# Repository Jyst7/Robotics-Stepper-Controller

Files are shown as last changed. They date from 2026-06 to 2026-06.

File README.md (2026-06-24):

# Robotics-Stepper-Controller

Screenshot 2026-06-23 at 11 46 33 PM

Screenshot 2026-06-23 at 11 47 46 PM

Screenshot 2026-06-23 at 11 48 07 PM

Screenshot 2026-06-23 at 11 48 39 PM

This project is a motor controller board and a cycloidal gearbox. It is designed around the esp32 s3 and can handle up to 6 nema 23's using dm542's.

## Main features

- ESP32 S3: allows for wifi and bluetooth connectivity aswell as allows programming using arduino ide

- up to 6 motors: allows for using up to 60 motors through the dm542 motor driver

- up to 8 inputs: allows for some electrically isolated inputs for limit switches probes, etc

- Sd card: not to sure what to use it for at the moment but its useful to have

- 3d printed cycloidal reducer: 1:10 ratio cycloidal gearbox designed to mount to a Keling KL23H276-30-4A stepper motor

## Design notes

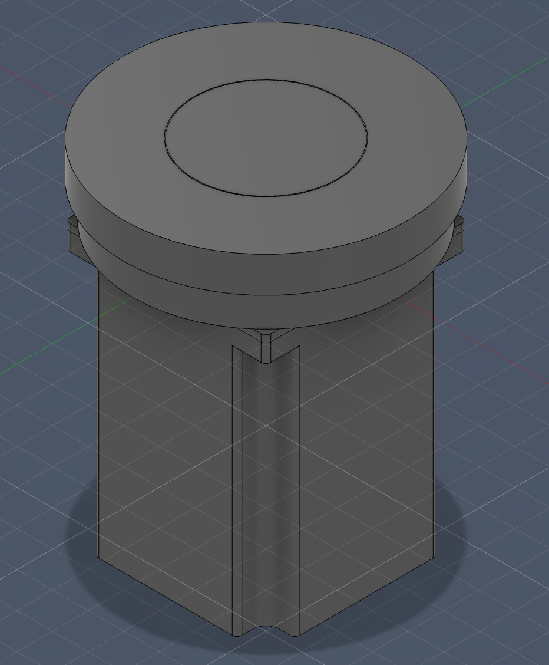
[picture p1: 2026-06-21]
Images/nema23-actuator.png

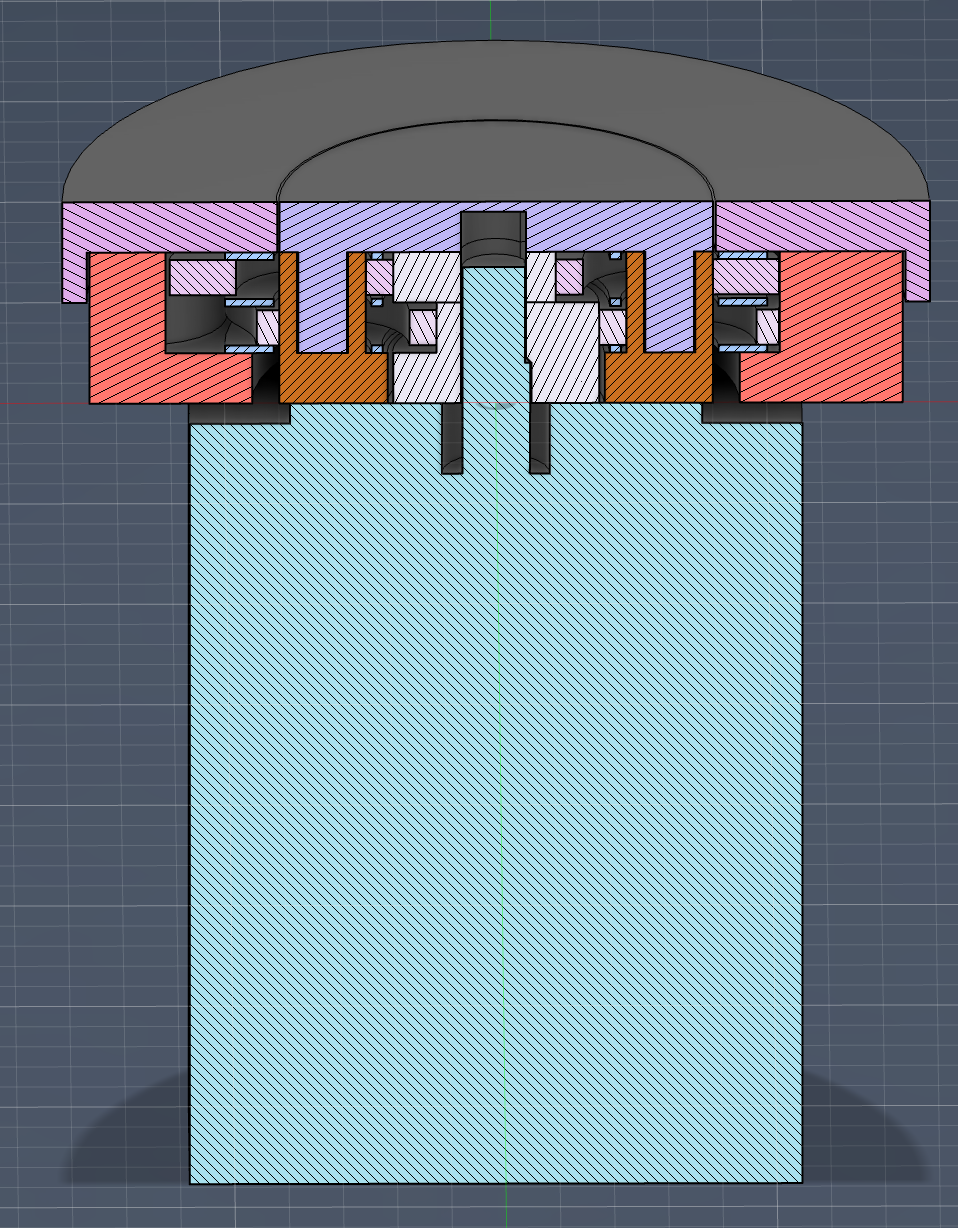
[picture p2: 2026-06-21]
Images/split-nema23-actuator.png

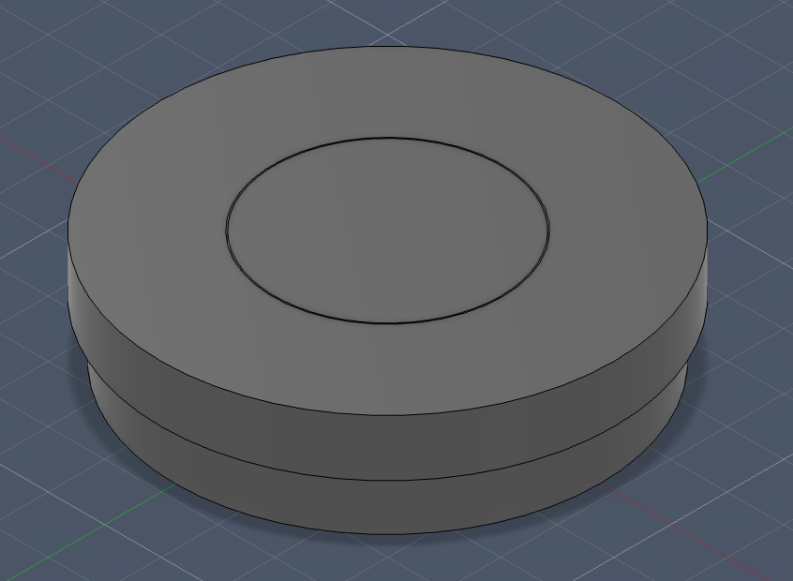
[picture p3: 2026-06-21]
Images/actuator.png

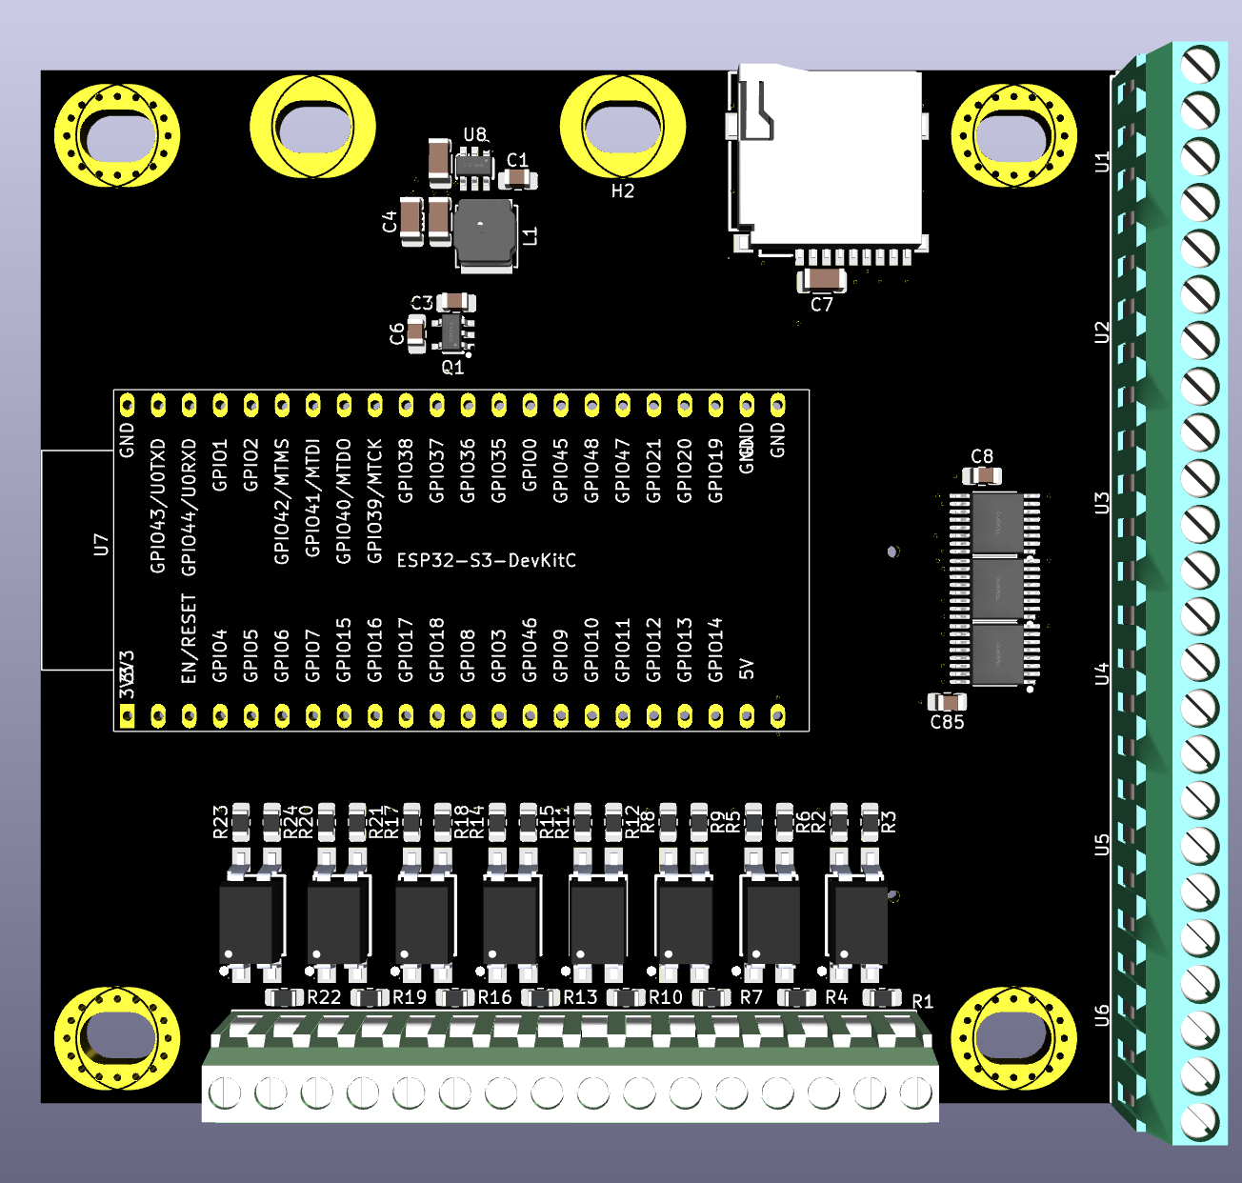
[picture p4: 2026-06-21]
Images/render-1.png

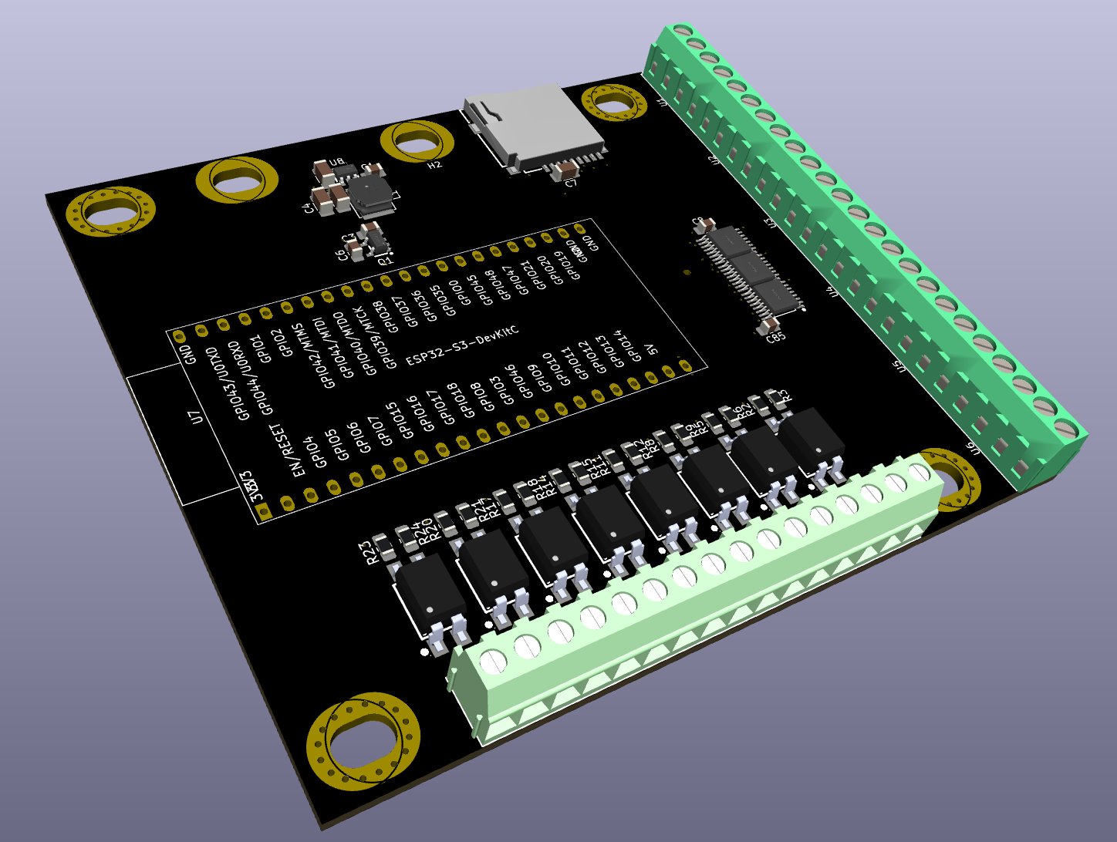
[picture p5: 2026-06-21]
Images/render-2.png

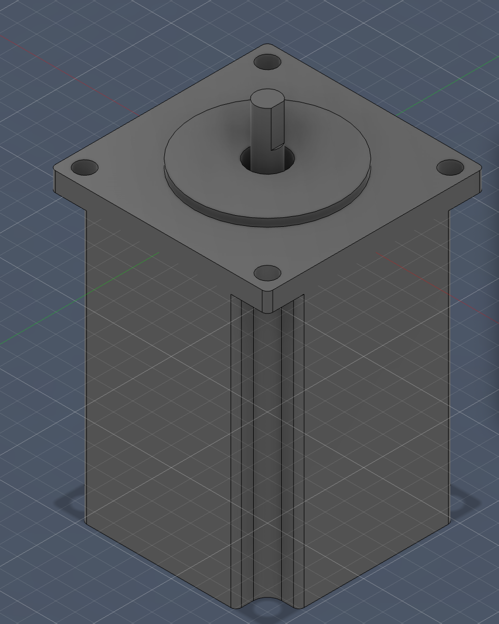
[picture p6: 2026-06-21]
Images/nema23.png

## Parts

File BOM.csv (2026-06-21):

BOM
Untitled
Reference | Qty | Value | DNP | Exclude from BOM | Exclude from Board | Footprint | Datasheet | LCSC Part | Price
U14,U18 | 2 | DB125-3.5-8P-GN-S |  |  |  | easyeda2kicad:CONN-TH_8P-P3.50_DORABO_DB125-3.5-8P-GN-S | https://www.lcsc.com/datasheet/C5184954.pdf | C5184954 | $1.30
U12,U16,U20 | 5 | 74AHCT595T16-13 |  |  |  | easyeda2kicad:TSSOP-16_L5.0-W4.4-P0.65-LS6.4-BL | https://lcsc.com/product-detail/presales_Diodes-Incorporated-74AHCT595T16-13_C460504.html | C460504 | $1.32
U10,U11,U13,U15,U17,U19,U21,U22 | 10 | TLP521GB-S_C20612587 |  |  |  | easyeda2kicad:SMD-4_L6.5-W4.6-P2.54-LS10.2-BL | https://www.lcsc.com/datasheet/C20612587.pdf | C20612587 | $1.10
U8 | 1 | AP63205WU-7 |  |  |  | easyeda2kicad:TSOT-23-6_L2.9-W1.6-P0.95-LS2.8-BL | https://www.lcsc.com/datasheet/C2071056.pdf | C2071056 | $0.44
U7 | 5 | ESP32-S3-DevKitC(PIN HEADERS) |  |  |  | PCM_Espressif:ESP32-S3-DevKitC | https://www.lcsc.com/datasheet/C7499337.pdf | C7499337 | $0.93
U1,U2,U3,U4,U5,U6 | 10 | DB125-3.5-4P-GN |  |  |  | easyeda2kicad:CONN-TH_DB125-3.5-4P-GN | https://www.lcsc.com/datasheet/C2757925.pdf | C2757925 | $3.37
R3,R6,R9,R12,R15,R18,R21,R24 | 20 | 10K |  |  |  | Resistor_SMD:R_0805_2012Metric_Pad1.20x1.40mm_HandSolder | https://www.lcsc.com/datasheet/C110775.pdf | C110775 | $0.78
R2,R5,R8,R11,R14,R17,R20,R23 | 20 | 1K |  |  |  | Resistor_SMD:R_0805_2012Metric_Pad1.20x1.40mm_HandSolder | https://www.lcsc.com/datasheet/C110774.pdf | C110774 | $0.79
R1,R4,R7,R10,R13,R16,R19,R22 | 10 | 300Ω |  |  |  | Resistor_SMD:R_0805_2012Metric_Pad1.20x1.40mm_HandSolder | https://www.lcsc.com/datasheet/C7603206.pdf | C7603206 | $3.45
Q1 | 1 | XC6220B331MR-G |  |  |  | easyeda2kicad:SOT-25_L3.0-W1.6-P0.95-LS2.8-TL | https://lcsc.com/product-detail/Low-Dropout-Regulators-LDO_XC6220B331MR-G_C86534.html | C86534 | $0.45
L1 | 10 | 4.7μH |  |  |  | easyeda2kicad:IND-SMD_L5.0-W5.0 | https://www.lcsc.com/datasheet/C520348.pdf | C520348 | $0.56
Card1 | 10 | TF PUSH |  |  |  | easyeda2kicad:TF-SMD_TF-PUSH | https://lcsc.com/product-detail/Connector-Card-Sockets_SHOU-HAN-SHOU-HAN-TFDeck-TF-Deck_C393941.html | C393941 | $1.26
C1,C7,C8,C85 | 50 | 0.1 μF |  |  |  | Capacitor_SMD:C_0805_2012Metric_Pad1.18x1.45mm_HandSolder | https://www.lcsc.com/datasheet/C49678.pdf | C49678 | $1.34
C7 | 50 | 100nF |  |  |  | Capacitor_SMD:C_1206_3216Metric | https://www.lcsc.com/datasheet/C309030.pdf | C309030 | $1.28
C6 | 10 | 4.7μF |  |  |  | Capacitor_SMD:C_0805_2012Metric_Pad1.18x1.45mm_HandSolder | https://www.lcsc.com/datasheet/C33546011.pdf | C33546011 | $0.78
C4,C5 | 10 | 22μF |  |  |  | Capacitor_SMD:C_1206_3216Metric | https://www.lcsc.com/datasheet/C342620.pdf | C342620 | $3.61
C2,C3 | 20 | 10μF |  |  |  | Capacitor_SMD:C_0805_2012Metric_Pad1.18x1.45mm_HandSolder | https://www.lcsc.com/datasheet/C1713.pdf | C1713 | $0.98
Total LCSC |  |  |  |  |  |  |  |  | $23.74
DM542 | 6 |  |  |  |  |  | https://www.aliexpress.com/item/1005005264850020.html |  | $32.94
Total Aliexpress |  |  |  |  |  |  |  |  | $32.94
Total Overall |  |  |  |  |  |  |  |  | $56.68

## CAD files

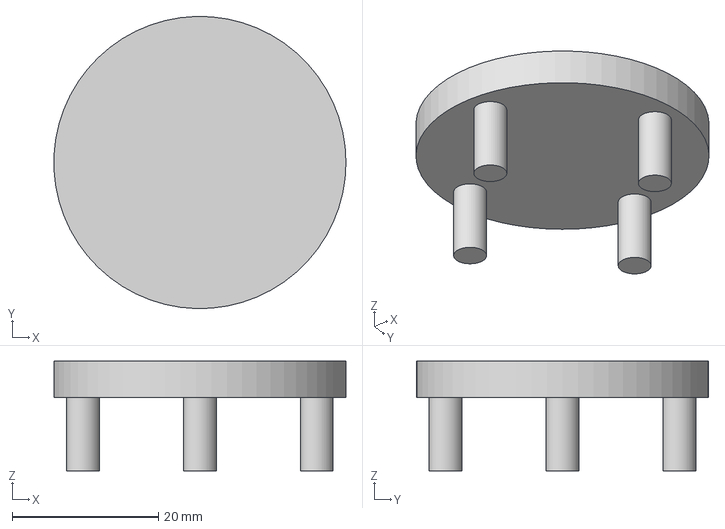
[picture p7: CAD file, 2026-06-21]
CAD/Component16.step
40.0 x 40.0 x 15.0 mm

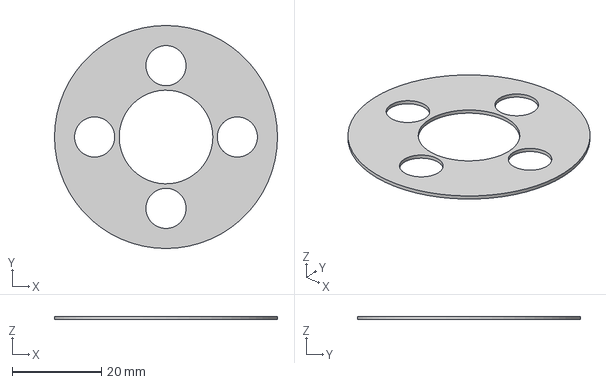
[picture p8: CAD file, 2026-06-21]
CAD/Spacer.step
50.0 x 50.0 x 0.75 mm

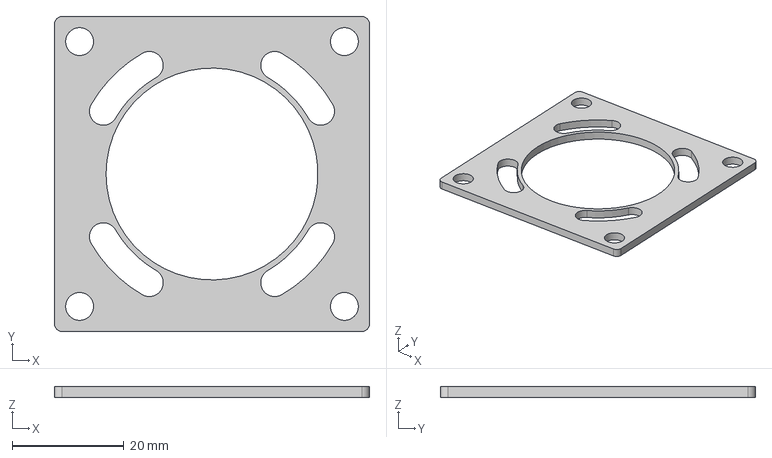
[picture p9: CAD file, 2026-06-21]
CAD/Cycloidal Drive.step
56.5 x 56.5 x 2.00 mm

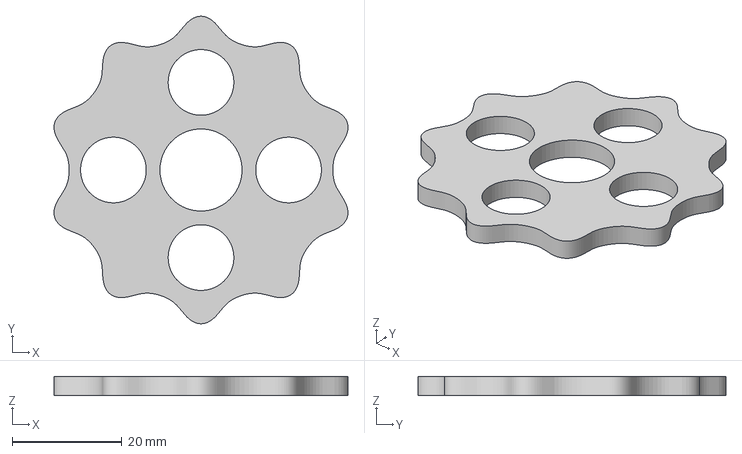
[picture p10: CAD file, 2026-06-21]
CAD/Component13.step
53.7 x 56.2 x 3.50 mm

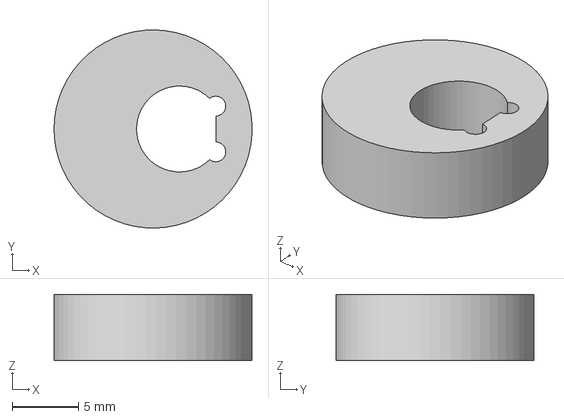
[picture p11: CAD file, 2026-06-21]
CAD/Component12-1.step
15.0 x 15.0 x 5.00 mm

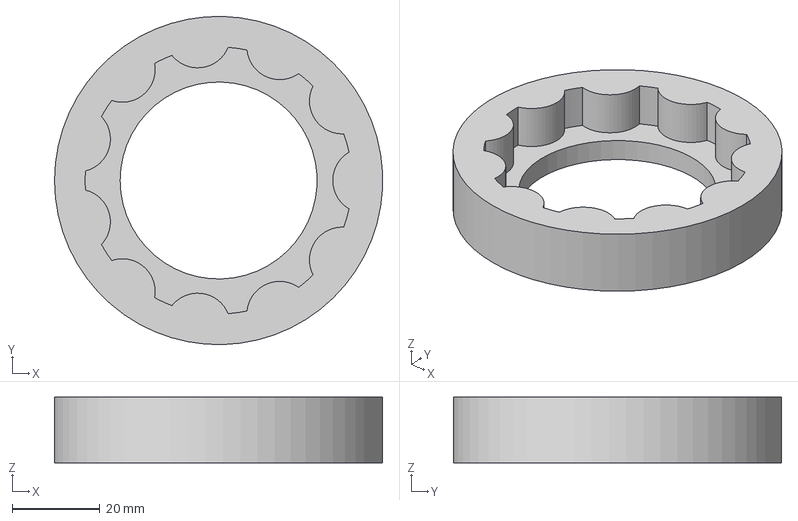
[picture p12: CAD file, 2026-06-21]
CAD/Component10.step
74.9 x 75.0 x 15.0 mm

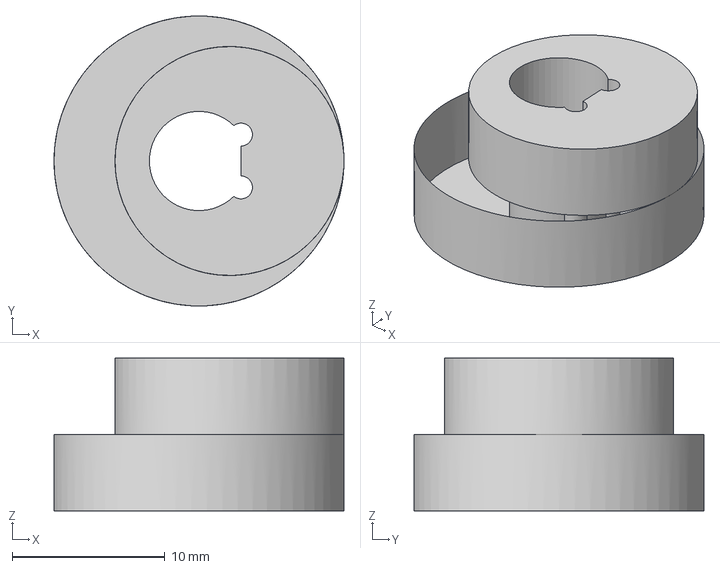
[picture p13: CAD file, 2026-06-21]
CAD/Component12.step
19.0 x 19.0 x 10.0 mm

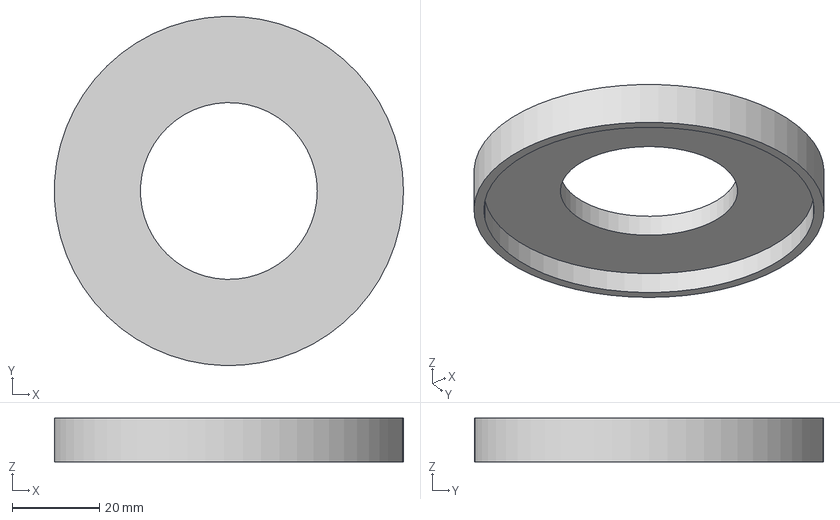
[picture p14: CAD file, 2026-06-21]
CAD/Component15.step
79.9 x 80.0 x 10.0 mm

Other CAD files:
CAD/Component11.step

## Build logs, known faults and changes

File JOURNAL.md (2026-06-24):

## Background - 0 Hours

The reason I decided to make this project was for two reasons, the first being I wanted to justify procrastinating studying for exams and I'd feel bad if I was just doomscrolling and the second is because I had 3 stepper motors lying around specifically the Keling Technology, Inc Hybrid Stepper Motor Type:KL23H276-30-4A. I would like to be able to use them and I recently got a power supply. I didn't really have any large constrainst for this project but I knew that I wanted to have the ability to add more motors later on as well as other peripherals that I might use in the future. I also wanted to under the guise of this project to make some simple cycloidal drives for the motors and see the extent of their strength. I later in the process decided it might be nice to attempt to turn this into a robotic arm because I find them cool, which in my opionion is a great reason. Also all parts should be purchased from Aliexpress, Lcsc, and Jlcpcb. I somehow forgot about the biggest constraint of all which is money, the goal is to keep it under $120 but if absolutely necessary could be stretched to $180 as I am making this for hackclub's outpost ysws.

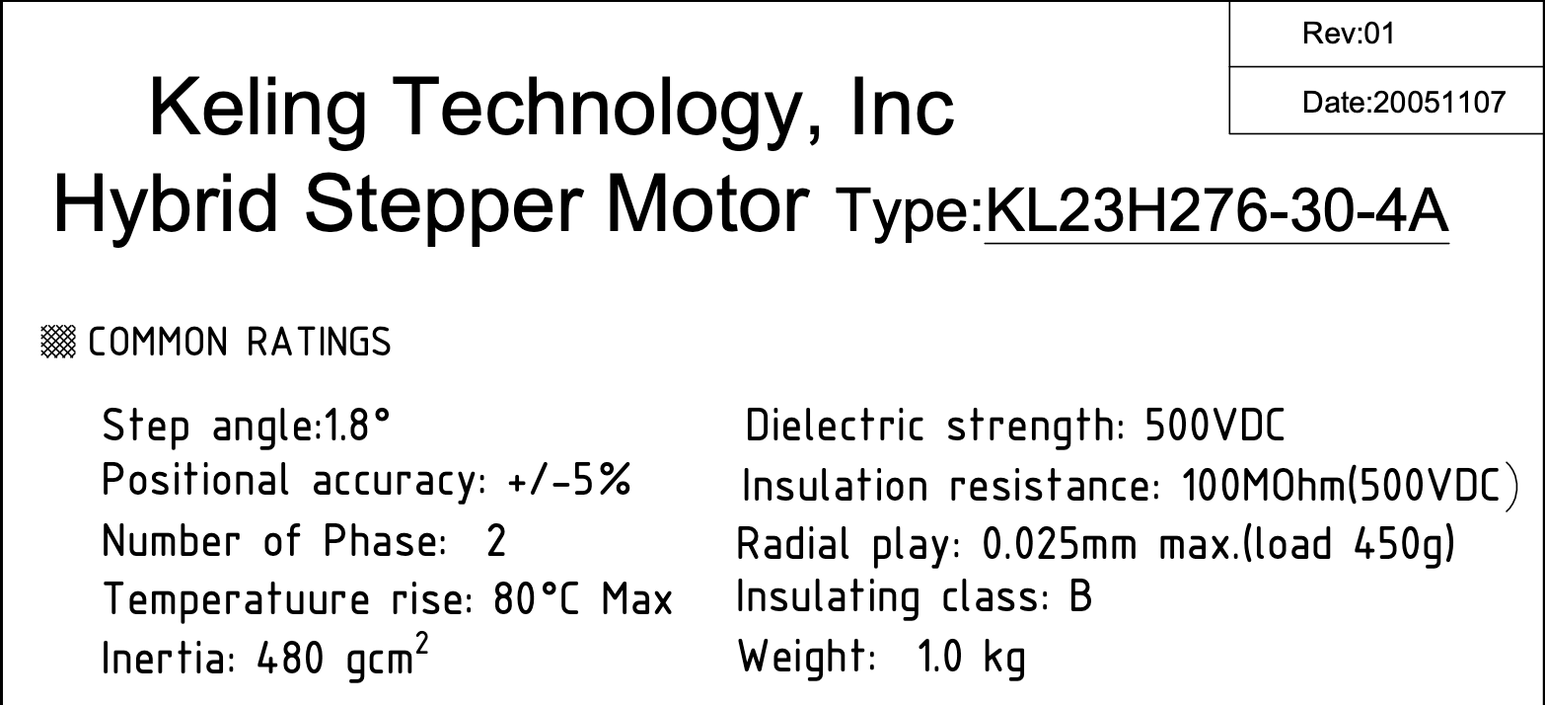
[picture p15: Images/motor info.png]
motor info


## Research - 3 Hours

The first thing I wanted to reasearch was the motor drivers I was going to use. I took a look at aliexpress just searching up stepper motor drivers and saw three different options which went down to two when I realized for this big motor it probably needs a decently large stepper driver for the heat and other things. So I threw all the data about the motors into google and apparently it is quite close to being a nema 23 motor which I found slightly weird based on the size differences, but google probably knows better than me because its twice the size of a nema 17. So the two motor drivers I decided between was the TB6600 and the DM542. It was not very difficult to decide between the two as almost every source online unanimously says the DM542 is better.

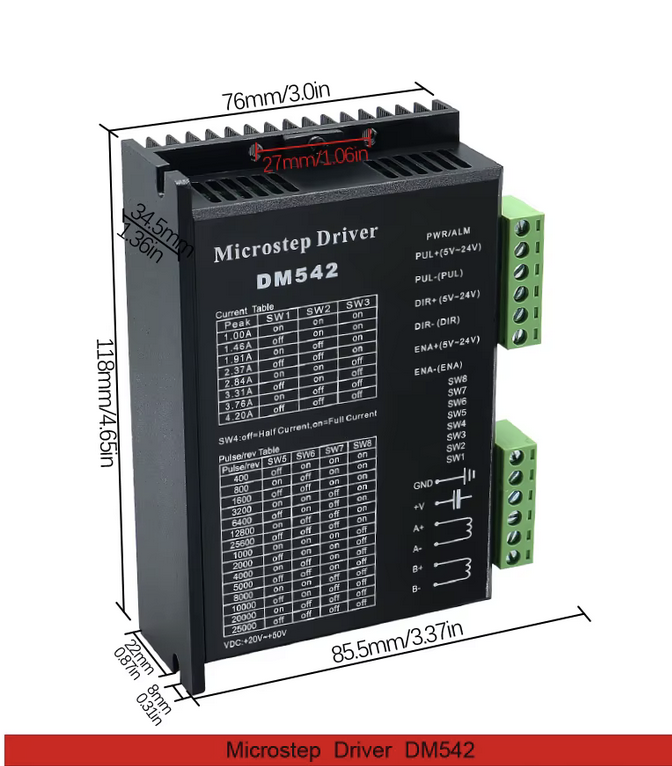
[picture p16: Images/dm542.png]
motor driver


I also took a look at many other different cnc controllers as I made the assumption that the board I am making is just a cnc controller without the logic and circuits for the spindle motor. I also was able to look at the controller boards for the large cnc machine and the small one that is in the shop at my school and other than the integrated psu and spindle motor stuff I had a good idea of what I needed to make to the board.

The microcontroller that I decided on was the esp32 s3 devkitc. Not only is this a decently powerful microcontroller, but it works with Arduino IDE which I found has integrated libraries for using stepper motors with the DM542. What was even better is I have two of these on hand so I could save some of my budget for other things. The esp32 also has integrated bluetooth and wifi capabilities so I could potentially make a webapp or something of the sort to connect to it and send commands to the motors, but the implementation for that will be later for now the goal is getting the motors to spin up.

Thinking about my 3d printer I decided an sd card is good to have because you never know when the need for the sd card could come up so some precautionary work is always good to have done.

I also wanted some optocouplers because I had seen them on some other boards and the purpose of them seems quite useful. They should mostly be electrically isolated from the rest of the board other than the 5v power which is fine so if something goes wrong and dumps a ton of voltage or current the optocoupler breaks or the 5v converter breaks and not the rest of the board. Thus allowing for safe addition of other inputs such as limit switches to not crash an axis if I'm doing something that has an axis, or probing a point in space.

For the power situation I decided to underpower my motors a bit because my psu can safely go up to 32V which is I believe the reccomended amound for nema 23 motors I didn't really want to go near the top range of my PSU's capabilities so I thought 24V would work fine they just wouldn't be as powerful as they could be. This also made powering the pcb slightly easier as I already had a buck converter in mind. So I would take the 24V from the psu and buck it down to 5V which can power some things that are fine with a bit of noise and then I could use an LDO to get a clean 3.3v to the SD card and the esp32 which don't like a lot of noise.

## Schematic - 4 Hours

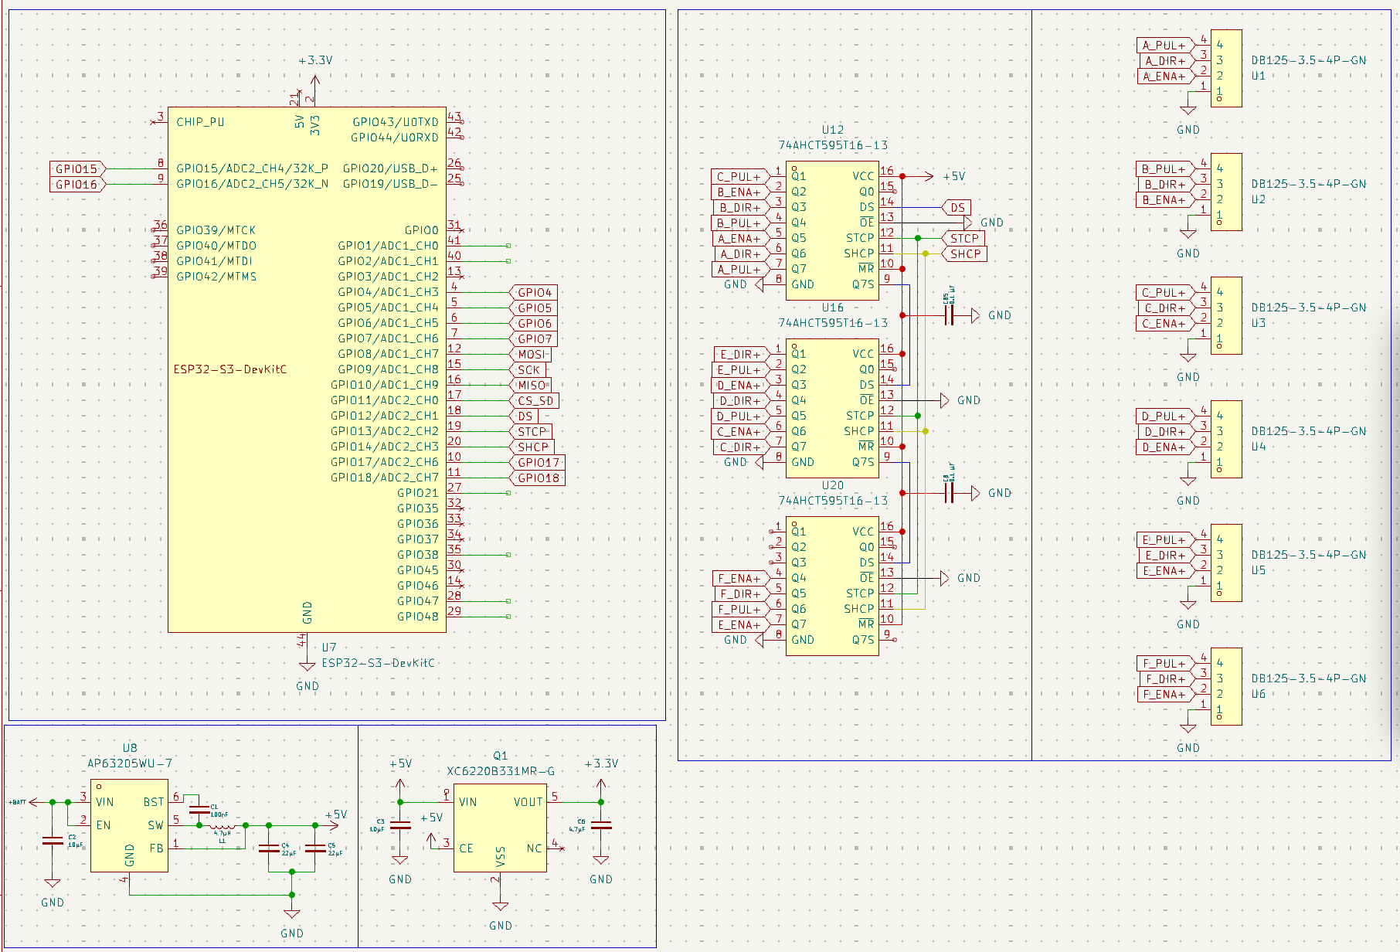
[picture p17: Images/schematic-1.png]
schematic

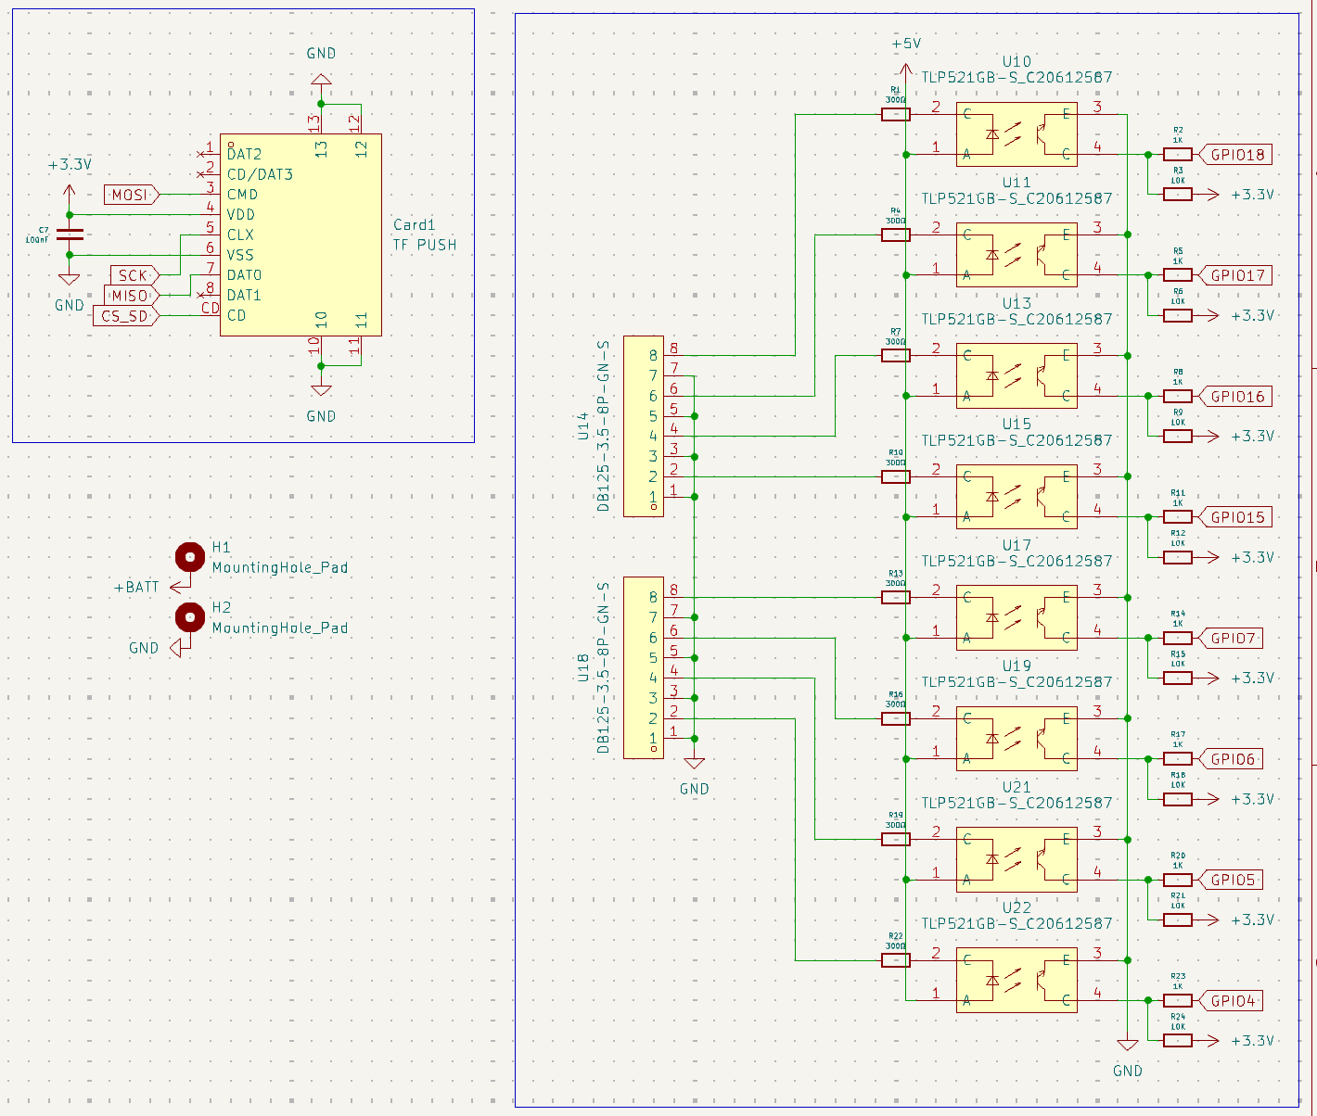
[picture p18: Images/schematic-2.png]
schematic


At this point in the project after all the research I had done I decided to just start doing the schematic. The first thing that I did was set up easyeda2kicad which is my savior for any kicad project because 90% of the lcsc parts I use have an easyeda footprint and schematic that can be ported over to kicad and it saves so much time that would be spent just making the symbols and footprints that 90% of the time I mess up when I make them custom. I threw in my parts starting with the esp32, the sd card, buck converter and ldo.

I started by putting together the buck converter and the ldo. These two components I have had lots of problems with in the past. So usually when I use them it ends up with the magic smoke being released from the devices and unfortunately you can't put that back in the component so I have often opted to just use a physical device that will give a stable 5v output and isolate the higher voltage, but this time I am pulling all the stops and found a popular buck converter that is specifically made with 12V and 24V in mind and following the schematic and reccomended component layout to a tee. Unfortunately for the LDO there is only a reccomended schematic so I followed that and I will have to figure out and get advice for the LDO part.

After this I threw up a bunch of screw terminals and immideately realized that the esp32 does not have enough pins for the optocouplers and 6 motors as each motor requires 3 pins to the motors PUL+ DIR+ and ENA+, ENA+ is slightly debatable because it could just be used for a software stop by pulling high, but if I really need to I can just cut power to the board, but if its an option might as well have it. So the only option rather than decide on a new microcontroller I just threw some shift registers on there and called it a day. I found that some shift registers I have used in the past will not work because it is recommended to use a specific one for this application. I don't remember the exact reason off the top of my head, but I think it was something about the communication being spi rather than i2c.

Then I threw together the optocouplers which I could not find any schematic advice or anything for so I found some other projects that used it, checked their use case and its implementation and then used their configuration and it should work for my use case as well.

## PCB - 2 Hours

Screenshot 2026-06-23 at 11 46 33 PM

I started routing the the buck converter according to the reccomended layout and I realized a bit late that two of the components had to be 1206 rather than the 0805 that I used so I had to redo the layout which was totally very fun. The LDO I kind of winged where I just routed overly large traces and added a bunch of ground vias, but from similar layouts for them that I have seen it should work.

Then I placed the rest of the footprints in the layout and organized them to the layout worked best and ajusted what gpios I would use. I had the screw terminals for the motors on one end, screw terminals for the optocouplers on the adjacent edge with the sd card and the power management on the top edge, with the esp32 on the left edge

With that done the rest of the wiring was simple, the only fancy-ish thing I added was decently large traces for the 5V and 3.3V.

## Code - 1.5 Hours

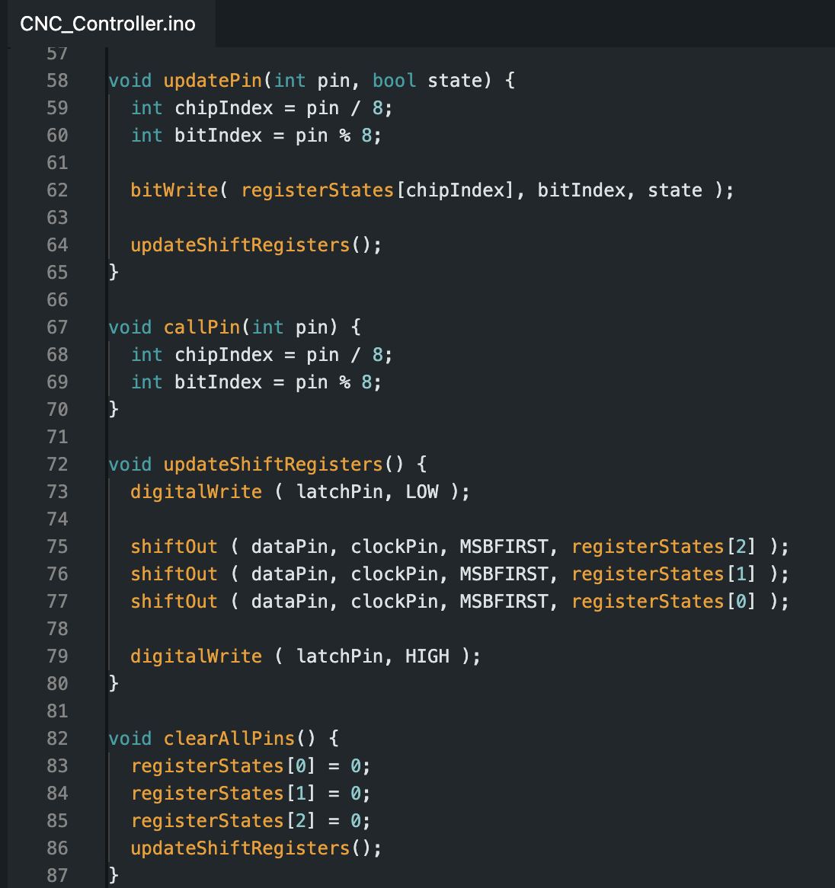
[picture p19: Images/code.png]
code


Code I will say is not my strongest suit, but I made a simple program that controls the motors. I started by using accelmotor which is a library that is used for controlling stepper motors through arduino ide. Unfortunately that does not work when using shift registers so I had to program it to work natively. With some research of the docs I found how to use the spi on the shift registers to then control the motors with the DIR+ and PUL+ pins. Then I just have it move backwards for a second and forwards for a second to test the motors.

The shift registers were extra interesting because three of them are daisy chained, and so I have to check which shift register the code connects to and then sends the proper output to the pin 1-7. The rest is pretty basic though for the main loop.

## CAD - 4 Hours

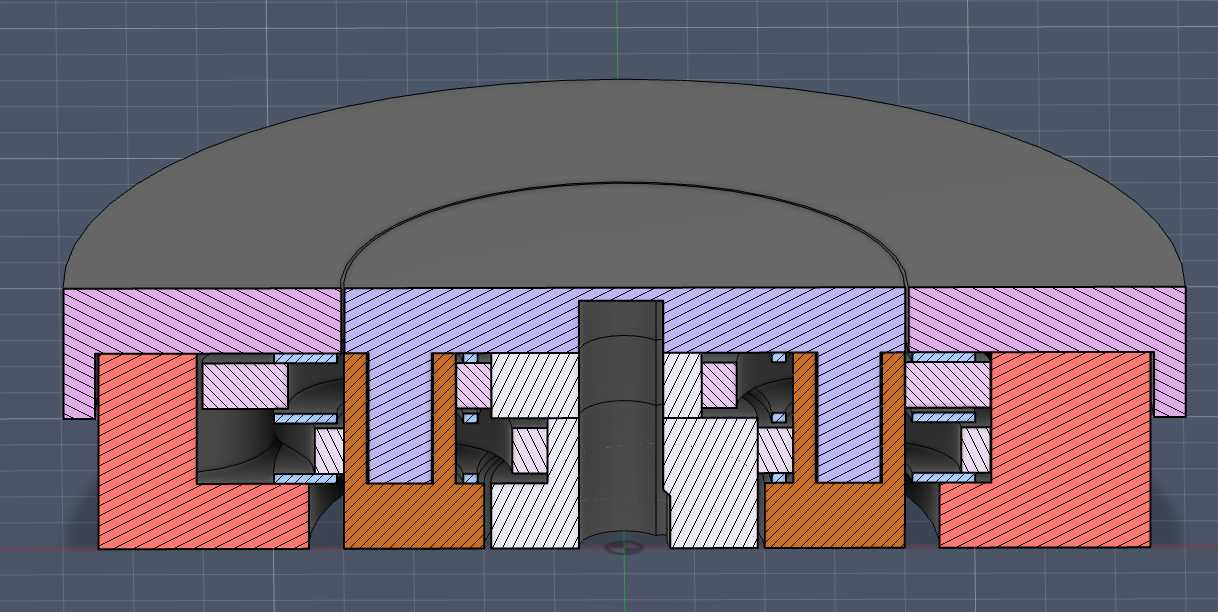
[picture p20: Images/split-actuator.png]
actuator


For the cad I had to start with making the motor itself because as I mentioned prior the motor is a different size compared to a regular nema 23. With my trusty old calipers I started to measure the motor and realized I had lost the battery cover so one quick makerworld search and print later I have working calipers. The measurements are kinda weird but I get it modelled. Naturally right after I measure it I remember about the site that has all the measurments for the motor and I didn't need to do it.

I then started by making a faceplate for the motor that will have a friction fit around the raised circle on the top and screws can go through to figure out the profile and have a surface for the rest of the cycloidal gearbox. I added some empty spaces around the main circle to allow for some flex to have a tighter fit. On my second iteration I got it to fit quite snugly without having too much of a struggle to put it on as well as the screws fit nicely self tapping into the plasitc.

For the next section I realized I didnt have a ton of filament left so I opted for not a huge reducer where the cycloid would be slightly less in diameter than the distance between screws on the motor. I opted for a simple 1:10 ratio I think thats the right order of numbers, but thats besides the point and used two cycloid disks. I was going to implement some new bearings I have gotten into this design but I realized at this scale it would be too difficult as everything is quite small. I wanted to focus on making the input and output tolerances as tight as i can as with 3d printing these reducers in the past I have found that they have some backlash just do to loose tolerances. I also attempted a different method of bearings this time opting for one that goes around the output pegs and centre disk between the bottom housing and the cycloid, the cycloid and the other cycloid, and the top cycloid and the top housing. Last time I made a similar reducer I just put individual washers on each peg and shaft and it got quite annoying to assemble and dissasemble so I am hoping I get the same benifits and none of the drawbacks, but only time will tell. I also am attempting to hold the output ring in place by connecting it through the reducer which I think will work quite well to not have the output fall off because now it is supported, but structurally the weakest point is that output because its directly where the layer lines are so I might attemt some jank setups in the future to see if I can print it in another orientation and have the quality not be awful. Then with a couple test prints and tweaks for tolerances the reducer was done.

## Checking - 1 Hour

I was able to get some advice from both the hackclub slack, and mainly the kicad discord server which definitely saved me a few headaches, and was releiving to hear that the design looks good with no obvious errors.

## Future - 0 Hours

In the future once I test everything works I plan to get more motors to power with this board and turn it into a full arm because I think robotic arms are awesome. I also plan to change the code to have an interface on my computer that I can connect to rather than just inputting static programs for the motors to move. The only other thing I can think of, off the top of my head is to improve the cycloidal gearbox design and maybe add an enclosure for all the elctronics depending on how big the motor drivers are.

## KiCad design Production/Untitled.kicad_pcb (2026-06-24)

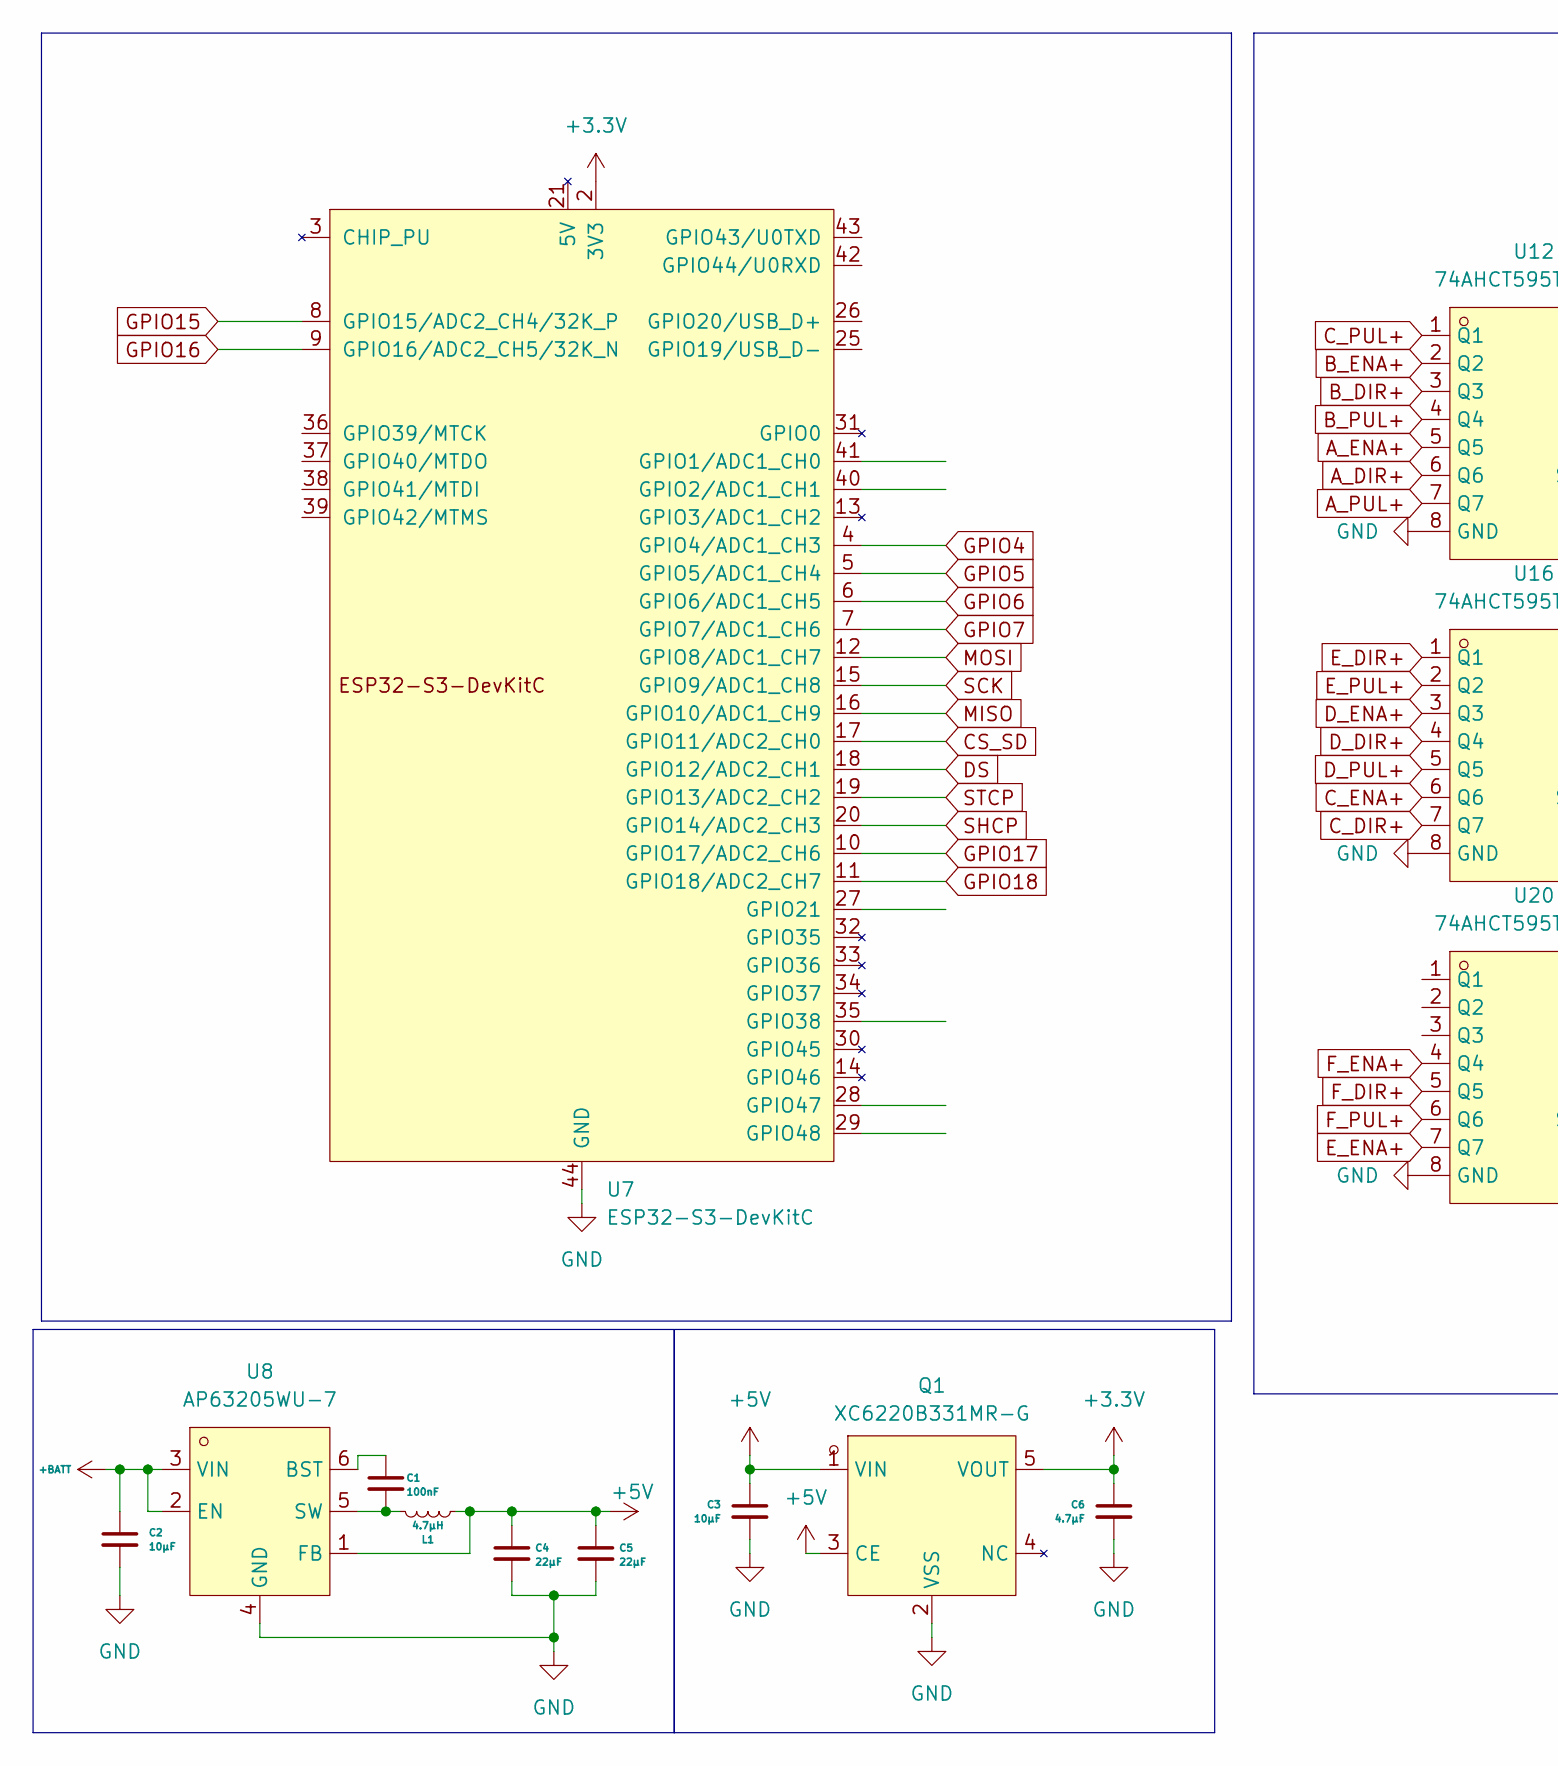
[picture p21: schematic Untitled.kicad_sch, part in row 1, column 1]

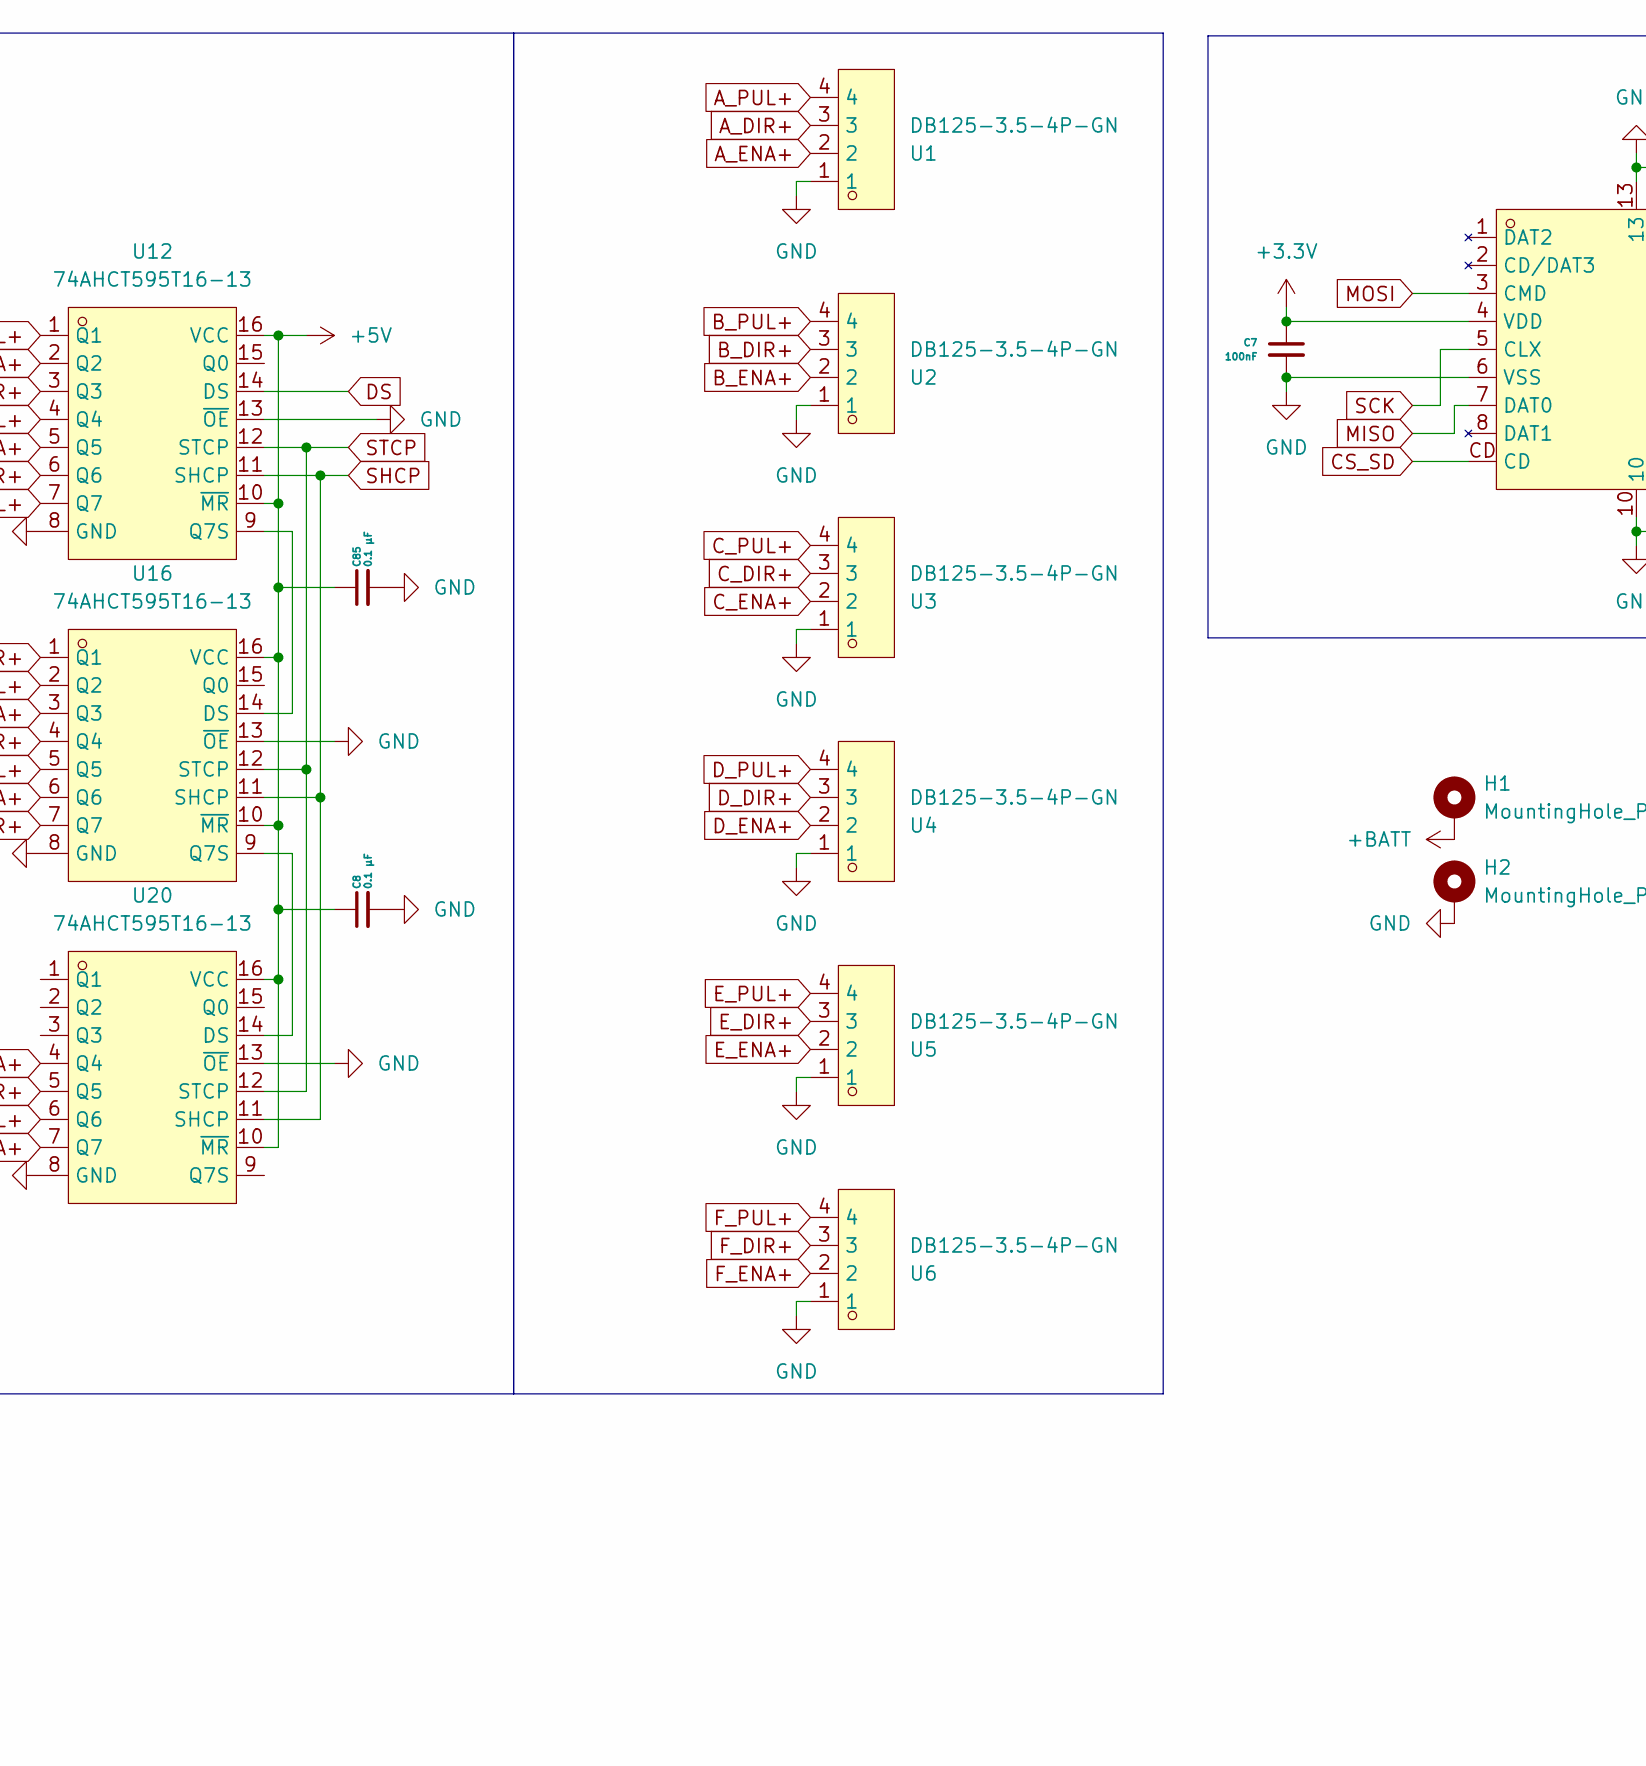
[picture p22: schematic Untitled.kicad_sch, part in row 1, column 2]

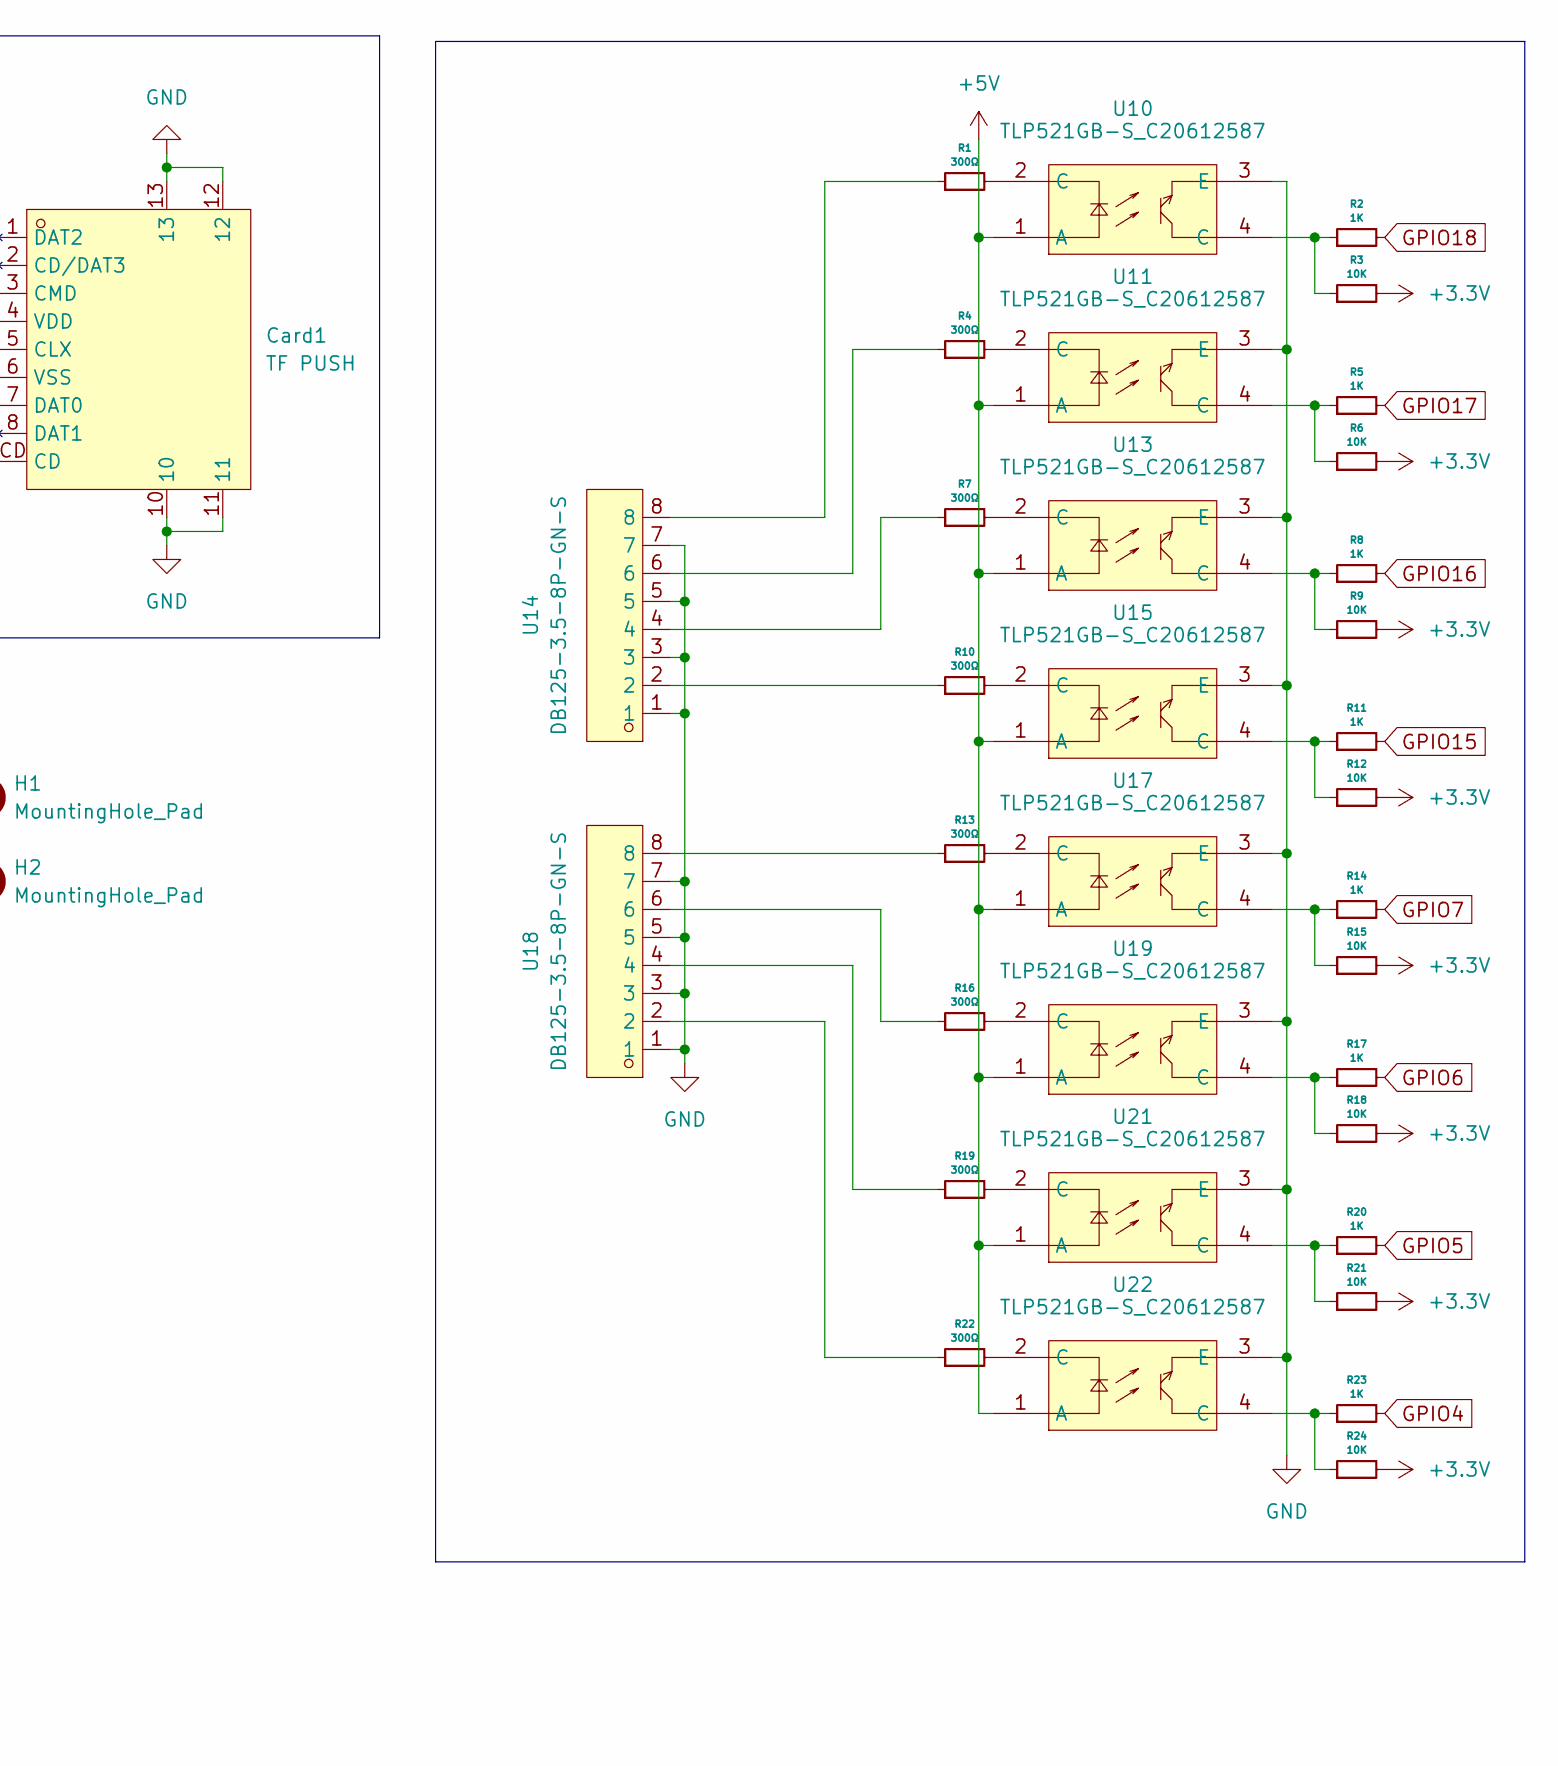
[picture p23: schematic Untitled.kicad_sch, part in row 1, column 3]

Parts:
C1: 100nF; C_0805_2012Metric_Pad1.18x1.45mm_HandSolder
C2: 10μF; C_1206_3216Metric
C3: 10μF; C_0805_2012Metric_Pad1.18x1.45mm_HandSolder
C4, C5: 22μF; C_1206_3216Metric
C6: 4.7μF; C_0805_2012Metric_Pad1.18x1.45mm_HandSolder
C7: 100nF; C_1206_3216Metric
C8, C85: 0.1 μF; C_0805_2012Metric_Pad1.18x1.45mm_HandSolder
Card1: TF PUSH; TF-SMD_TF-PUSH; MPN TF PUSH; LCSC Part C393941
H1, H2: MountingHole_Pad; MountingHole_4.3x6.2mm_M4_Pad
L1: 4.7μH; IND-SMD_L5.0-W5.0
Q1: XC6220B331MR-G; SOT-25_L3.0-W1.6-P0.95-LS2.8-TL; MPN XC6220B331MR-G; LCSC Part C86534
R1, R4, R7, R10, R13, R16, R19, R22: 300Ω; R_0805_2012Metric_Pad1.20x1.40mm_HandSolder
R2, R5, R8, R11, R14, R17, R20, R23: 1K; R_0805_2012Metric_Pad1.20x1.40mm_HandSolder
R3, R6, R9, R12, R15, R18, R21, R24: 10K; R_0805_2012Metric_Pad1.20x1.40mm_HandSolder
U1, U2, U3, U4, U5, U6: DB125-3.5-4P-GN; CONN-TH_DB125-3.5-4P-GN; MPN DB125-3.5-4P-GN-S; LCSC Part C2757925
U7: ESP32-S3-DevKitC
U8: AP63205WU-7; TSOT-23-6_L2.9-W1.6-P0.95-LS2.8-BL; MPN AP63205WU-7; LCSC Part C2071056
U10, U11, U13, U15, U17, U19, U21, U22: TLP521GB-S_C20612587; SMD-4_L6.5-W4.6-P2.54-LS10.2-BL; MPN TLP521GB-S; LCSC Part C20612587
U12, U16, U20: 74AHCT595T16-13; TSSOP-16_L5.0-W4.4-P0.65-LS6.4-BL; MPN 74AHCT595T16-13; LCSC Part C460504
U14, U18: DB125-3.5-8P-GN-S; CONN-TH_8P-P3.50_DORABO_DB125-3.5-8P-GN-S; MPN DB125-3.5-8P-GN-S; LCSC Part C5184954

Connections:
+3.3V: C6.1, C7.1, Card1.4 (VDD), Q1.5 (VOUT), R3.2, R6.2, R9.2, R12.2, R15.2, R18.2, R21.2, R24.2, U7.1 (3V3), U7.2 (3V3)
+5V: C3.1, C4.1, C5.1, C8.1, C85.1, L1.2, Q1.1 (VIN), Q1.3 (CE), U8.1 (FB), U10.1 (A), U11.1 (A), U12.10 (~MR), U12.16 (VCC), U13.1 (A), U15.1 (A), U16.10 (~MR), U16.16 (VCC), U17.1 (A), U19.1 (A), U20.10 (~MR), U20.16 (VCC), U21.1 (A), U22.1 (A)
+BATT: C2.1, H1.1, U8.2 (EN), U8.3 (VIN)
A_DIR+: U1.3, U12.6 (Q6)
A_ENA+: U1.2, U12.5 (Q5)
A_PUL+: U1.4, U12.7 (Q7)
B_DIR+: U2.3, U12.3 (Q3)
B_ENA+: U2.2, U12.2 (Q2)
B_PUL+: U2.4, U12.4 (Q4)
CS_SD: Card1.CD, U7.17 (GPIO11/ADC2_CH0)
C_DIR+: U3.3, U16.7 (Q7)
C_ENA+: U3.2, U16.6 (Q6)
C_PUL+: U3.4, U12.1 (Q1)
DS: U7.18 (GPIO12/ADC2_CH1), U12.14 (DS)
D_DIR+: U4.3, U16.4 (Q4)
D_ENA+: U4.2, U16.3 (Q3)
D_PUL+: U4.4, U16.5 (Q5)
E_DIR+: U5.3, U16.1 (Q1)
E_ENA+: U5.2, U20.7 (Q7)
E_PUL+: U5.4, U16.2 (Q2)
F_DIR+: U6.3, U20.5 (Q5)
F_ENA+: U6.2, U20.4 (Q4)
F_PUL+: U6.4, U20.6 (Q6)
GND: C2.2, C3.2, C4.2, C5.2, C6.2, C7.2, C8.2, C85.2, Card1.6 (VSS), Card1.10, Card1.11, Card1.12, Card1.13, H2.1, Q1.2 (VSS), U1.1, U2.1, U3.1, U4.1, U5.1, U6.1, U7.22 (GND), U7.23 (GND), U7.24 (GND), U7.44 (GND), U8.4 (GND), U10.3 (E), U11.3 (E), U12.8 (GND), U12.13 (~OE), U13.3 (E), U14.1, U14.3, U14.5, U14.7, U15.3 (E), U16.8 (GND), U16.13 (~OE), U17.3 (E), U18.1, U18.3, U18.5, U18.7, U19.3 (E), U20.8 (GND), U20.13 (~OE), U21.3 (E), U22.3 (E)
GPIO4: R23.2, U7.4 (GPIO4/ADC1_CH3)
GPIO5: R20.2, U7.5 (GPIO5/ADC1_CH4)
GPIO6: R17.2, U7.6 (GPIO6/ADC1_CH5)
GPIO7: R14.2, U7.7 (GPIO7/ADC1_CH6)
GPIO15: R11.2, U7.8 (GPIO15/ADC2_CH4/32K_P)
GPIO16: R8.2, U7.9 (GPIO16/ADC2_CH5/32K_N)
GPIO17: R5.2, U7.10 (GPIO17/ADC2_CH6)
GPIO18: R2.2, U7.11 (GPIO18/ADC2_CH7)
MISO: Card1.7 (DAT0), U7.16 (GPIO10/ADC1_CH9)
MOSI: Card1.3 (CMD), U7.12 (GPIO8/ADC1_CH7)
unnamed: R1.1, U14.8
unnamed: R1.2, U10.2 (C)
unnamed: R2.1, R3.1, U10.4 (C)
unnamed: R4.1, U14.6
unnamed: R4.2, U11.2 (C)
unnamed: R5.1, R6.1, U11.4 (C)
unnamed: R7.1, U14.4
unnamed: R7.2, U13.2 (C)
unnamed: R8.1, R9.1, U13.4 (C)
unnamed: R10.1, U14.2
unnamed: R10.2, U15.2 (C)
unnamed: R11.1, R12.1, U15.4 (C)
unnamed: R13.1, U18.8
unnamed: R13.2, U17.2 (C)
unnamed: R14.1, R15.1, U17.4 (C)
unnamed: R16.1, U18.6
unnamed: R16.2, U19.2 (C)
unnamed: R17.1, R18.1, U19.4 (C)
unnamed: R19.1, U18.4
unnamed: R19.2, U21.2 (C)
unnamed: R20.1, R21.1, U21.4 (C)
unnamed: R22.1, U18.2
unnamed: R22.2, U22.2 (C)
unnamed: R23.1, R24.1, U22.4 (C)
unnamed: C1.1, U8.6 (BST)
unnamed: C1.2, L1.1, U8.5 (SW)
unnamed: U12.9 (Q7S), U16.14 (DS)
unnamed: U16.9 (Q7S), U20.14 (DS)
SCK: Card1.5 (CLX), U7.15 (GPIO9/ADC1_CH8)
SHCP: U7.20 (GPIO14/ADC2_CH3), U12.11 (SHCP), U16.11 (SHCP), U20.11 (SHCP)
STCP: U7.19 (GPIO13/ADC2_CH2), U12.12 (STCP), U16.12 (STCP), U20.12 (STCP)

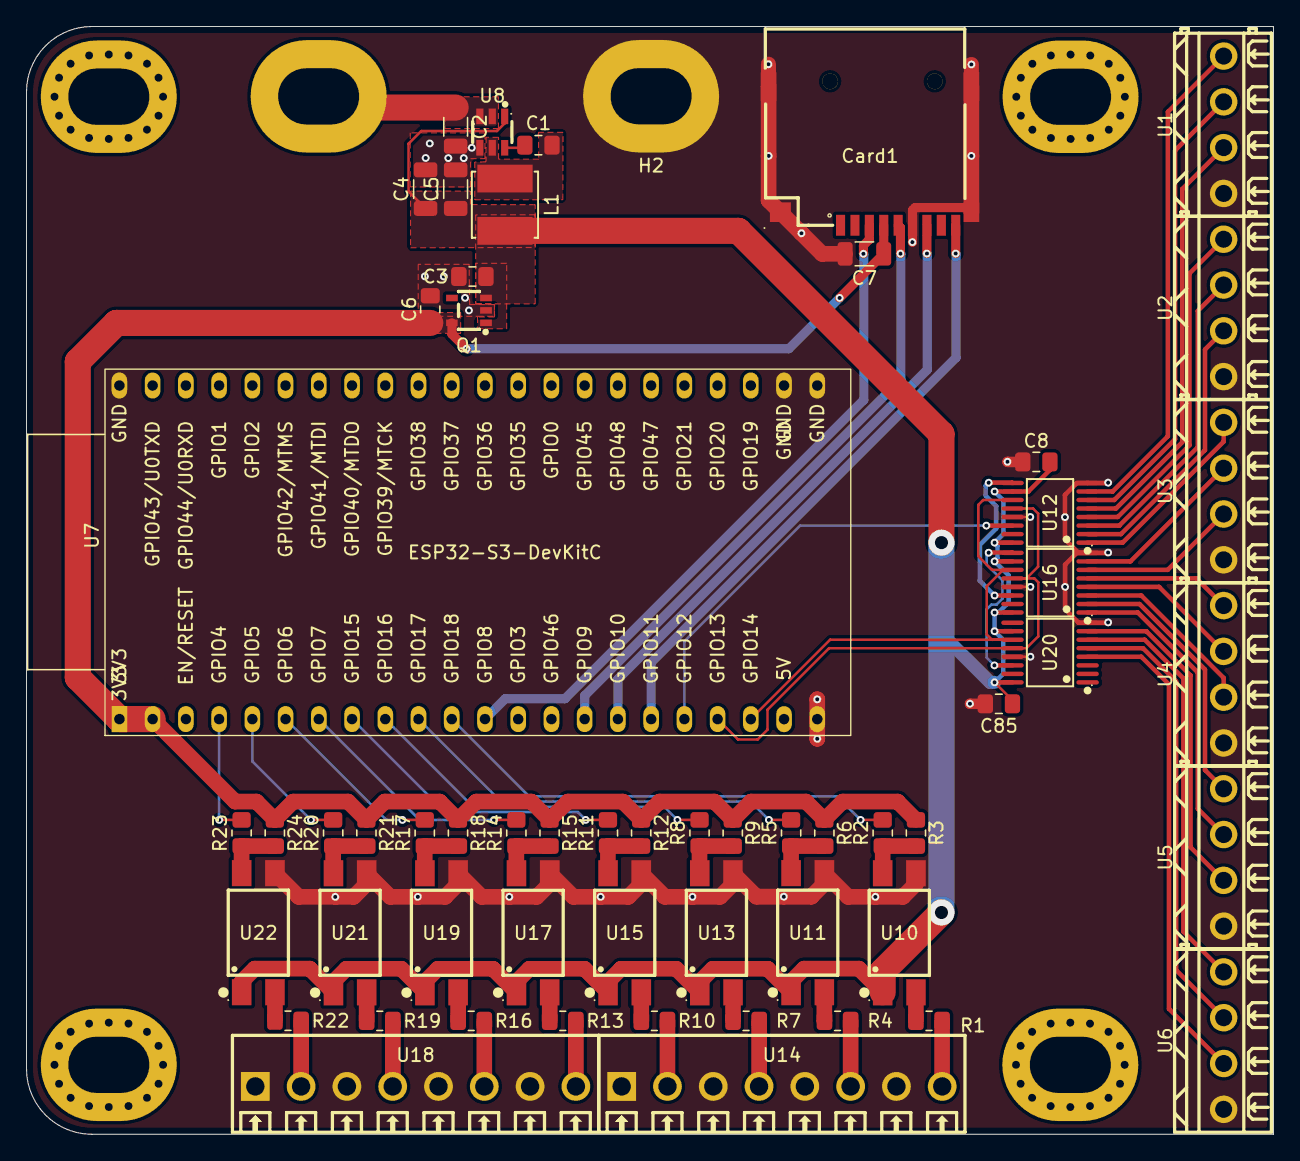
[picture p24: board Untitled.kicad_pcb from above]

Board: 2 copper layers, 95.3 x 84.7 mm, 59 parts (1 on the bottom side), 65 nets.

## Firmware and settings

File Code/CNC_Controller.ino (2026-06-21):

// shift register pins
const int dataPin = 12; // DS
const int latchPin = 13; // STCP
const int clockPin = 14; // SHCP

byte registerStates[3] = {0, 0, 0};

// virtual stepper pins
const int STEPPER1_PUL_PIN = 7;
const int STEPPER1_DIR_PIN = 6;

const int STEPPER2_PUL_PIN = 4;
const int STEPPER2_DIR_PIN = 3;

const int STEPPER3_PUL_PIN = 1;
const int STEPPER3_DIR_PIN = 9;

void setup() {
  // shift register pins
  pinMode ( dataPin, OUTPUT );
  pinMode ( latchPin, OUTPUT );
  pinMode ( clockPin, OUTPUT );

  clearAllPins();
}

void loop() {
  //motor test block

  // set direction
  updatePin(STEPPER1_DIR_PIN, HIGH);

  for(int i = 0; i < 200; i++) {
    updatePin(STEPPER1_PUL_PIN, HIGH);
    delayMicroseconds(800);
    
    updatePin(STEPPER1_PUL_PIN, LOW);
    delayMicroseconds(800);
  }

  delay(1000); // Wait 1 second
  
  // opposite direction
  updatePin(STEPPER1_DIR_PIN, LOW);
  
  for(int i = 0; i < 200; i++) {
    updatePin(STEPPER1_PUL_PIN, HIGH);
    delayMicroseconds(800);
    
    updatePin(STEPPER1_PUL_PIN, LOW);
    delayMicroseconds(800);
  }

  delay(1000);
  
}

void updatePin(int pin, bool state) {
  int chipIndex = pin / 8;
  int bitIndex = pin % 8;

  bitWrite( registerStates[chipIndex], bitIndex, state );

  updateShiftRegisters();
}

void callPin(int pin) {
  int chipIndex = pin / 8;
  int bitIndex = pin % 8;
}

void updateShiftRegisters() {
  digitalWrite ( latchPin, LOW );

  shiftOut ( dataPin, clockPin, MSBFIRST, registerStates[2] );
  shiftOut ( dataPin, clockPin, MSBFIRST, registerStates[1] );
  shiftOut ( dataPin, clockPin, MSBFIRST, registerStates[0] );

  digitalWrite ( latchPin, HIGH );
}

void clearAllPins() {
  registerStates[0] = 0;
  registerStates[1] = 0;
  registerStates[2] = 0;
  updateShiftRegisters();
}
